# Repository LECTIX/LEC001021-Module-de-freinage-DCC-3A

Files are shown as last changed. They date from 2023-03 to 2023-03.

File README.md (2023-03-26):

# LEC001021-Module-de-freinage-DCC-3A
Fichiers sources pour le produit LEC001021

## Description du produit

Arrêtez et redémarrez vos convois de manière automatique et réaliste avec des arrêts et redémarrages progressifs des trains.
- **Technologie ABC**
- **Courrant maximum** de 3A.
- **Compatibilité DCC uniquement** (digital). Les décodeurs doivent être compatible avec la technologie ABC ([Cf. notice](docs/manual_fr.pdf)).

## Utiliser les fichiers sources pour fabriquer le produit

Il n'est **pas nécessaire de savoir souder ou d'être bon en électronique** pour se procurer ce produit. Grâce aux fichiers sources publiés ici, vous pouvez être en mesure de faire fabriquer ce produit par un sous traitant.

### Faire fabriquer chez un sous traitant

Il est aujourd'hui possible de faire fabriquer à moindre cout des cartes électroniques. Nous recommendons [JLCPCB](https://jlcpcb.com/) si vous voulez aller au moins cher. Si vous préférez un acteur européen, [eurocircuits](https://www.eurocircuits.com/) est un des acteurs reconnus.

IMAGE ALT TEXT (http://www.youtube.com/watch?v=RXGGvsUtz0c "TUTO : faire fabriquer un produit LECTIX")

1. Télécherger les sources de ce produit en cliquant sur le bouton `Code`, puis `Download ZIP`.
1. Décompresser le dossier.
1. Les fichiers pour la fabrication se trouvent dans le répertoire `hardware/prod`.
1. Se connecter sur [https://cart.jlcpcb.com/quote](https://cart.jlcpcb.com/quote)
1. Cliquer sur le bouton `Add gerber file` et sélectionner le fichier `gerbers.zip`.
1. Sélectionnez la quantité de cartes que vous souhaitez dans le champs `PCB Qty`.
1. Laisser toutes les autres options par défaut, puis cliquez sur le toggle switch en face de `PCB Assembly`, et enfin sur le bouton `confirm`.
1. Une preview de la carte électronique sans les composants doit apparaitre. Cliquez sur `NEXT`.
1. Cliquez sur le bouton `Add BOM File`, puis sélectionnez le fichier `bom.csv`
1. Cliquez sur le bouton `Add CPL File`, puis sélectionnez le fichier `pos.csv`
1. **Vérifier que tous les composants sont en stock** et bien sélectionnés, puis cliquez sur `NEXT`.
1. Une preview de la carte avec ses composants apparait. Continuer le chemin en cliquant sur `NEXT`.
1. Le prix final apparait. Sélectionnez la catégorie du produit, puis cliquez sur `SAVE TO CART`.
1. Une fois sauvegardé dans votre panier, vous pouvez valider votre commande et choisir le moyen d'acheminement. Afin de ne pas avoir à se préoccuper des frais de douane, nous vous conseillons de choisir une méthode d'expédition DDP.

Vous receverez vos cartes sous 1 à 3 semaines. 

**Nous ne sommes en aucun cas responsables des cartes qui arriveraient défectueuses ou non fonctionnelles.**

### Modifications des fichiers sources

Installez kicad 6 (ou version supérieure), et ouvrez le fichier LEC001021.kicad_pro

### Regénérer les fichiers gerber, BOM, et position (Optionnel)

Peut se faire simplement en utilisant kikit :

```
cd hardware

docker run --rm -w /kikit -v $PWD:/kikit yaqwsx/kikit kikit fab jlcpcb --assembly --no-drc --schematic LEC001021.kicad_sch --field LCSC --corrections JLCPCB_CORRECTION --nametemplate LEC001021_{} LEC001021.kicad_pcb prod/

```
## Notices
[Manuel FR](docs/manual_fr.pdf)

[Manuel EN](docs/manual_en.pdf)

[Manuel DE](docs/manual_de.pdf)
## License
Tous nos fichiers sont plubliés sous la license CERN Open Hardware Licence Version 2 - Strongly Reciprocal

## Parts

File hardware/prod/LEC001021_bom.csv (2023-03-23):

Comment | Designator | Footprint | LCSC
RS3M | D1,D2,D4,D5 | Diode_SMD:D_SMC | C330389
SS34C | D3 | Diode_SMD:D_SMC | C13763
Screw_Terminal_01x02_blue | J1 | 0_connectors:TerminalBlock_bornier-2_P5.08mm-blue | C395882
logo_lectix_25mm | LOGO1 | 0_logos:Logo_10mm

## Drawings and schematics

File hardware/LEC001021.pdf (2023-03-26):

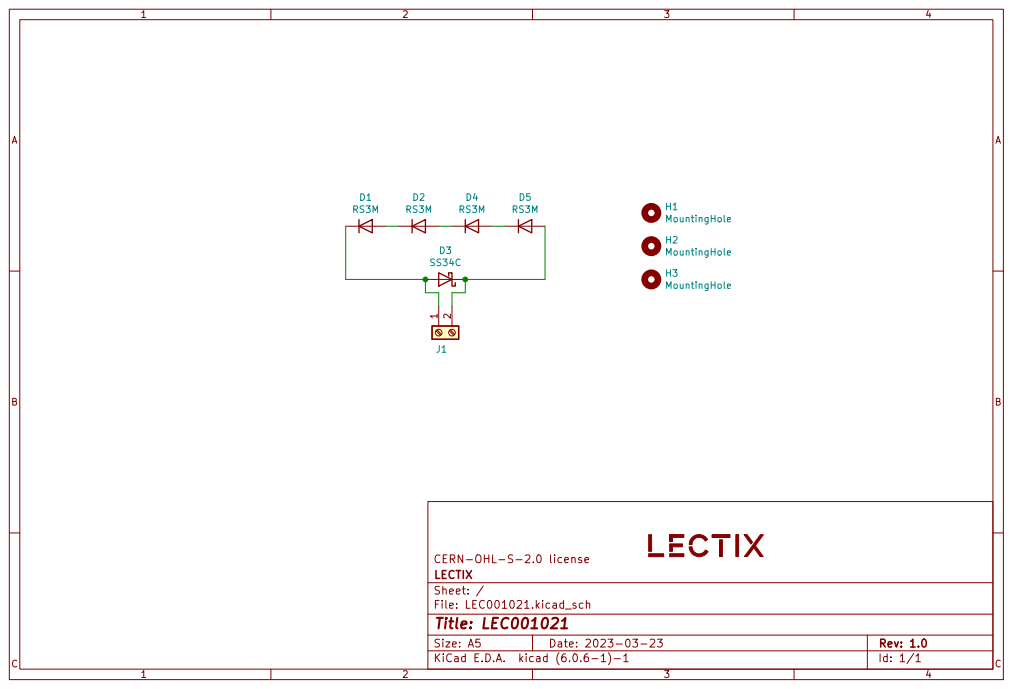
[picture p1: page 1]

File: LEC001021.kicad_sch Sheet: / LECTIX CERN-OHL-S-2.0 license D2 RS3M

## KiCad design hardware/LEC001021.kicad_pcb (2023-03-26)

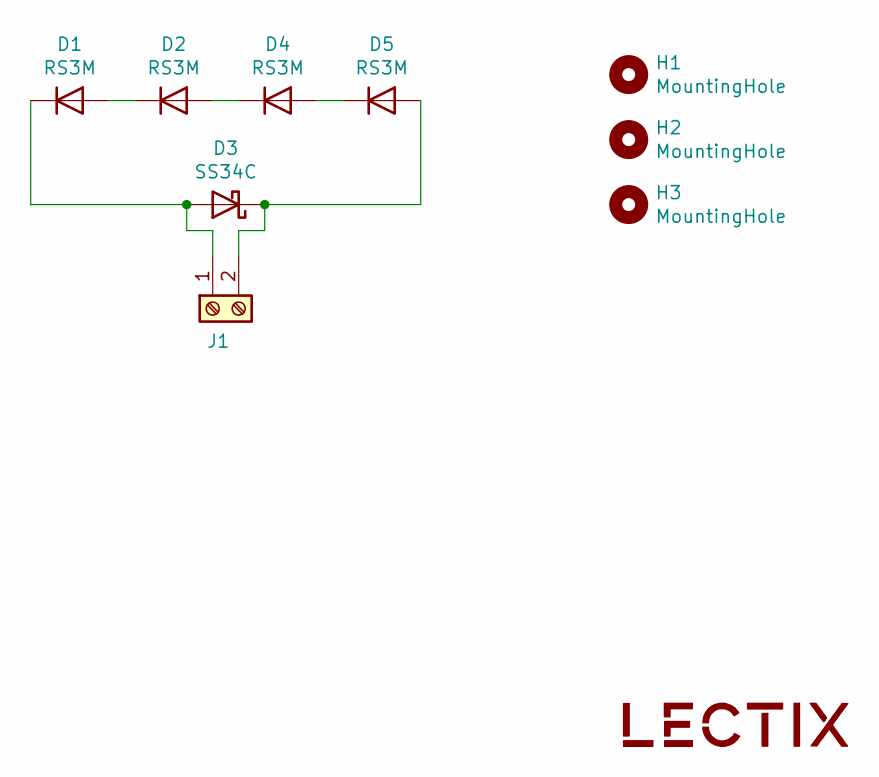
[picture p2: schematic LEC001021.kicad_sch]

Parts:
D1, D2, D4, D5: RS3M; D_SMC; MPN RS3M; LCSC C330389
D3: SS34C; D_SMC; MPN SS34C; LCSC C13763
H1, H2, H3: MountingHole; MountingHole_3.2mm_M3
J1: Screw_Terminal_01x02_blue; TerminalBlock_bornier-2_P5.08mm-blue; MPN DB301V-5.0-2P-BU-S; LCSC C395882
LOGO1: logo_lectix_25mm; Logo_10mm

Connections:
unnamed: D1.1 (K), D3.2 (A), J1.1
unnamed: D1.2 (A), D2.1 (K)
unnamed: D2.2 (A), D4.1 (K)
unnamed: D3.1 (K), D5.2 (A), J1.2
unnamed: D4.2 (A), D5.1 (K)

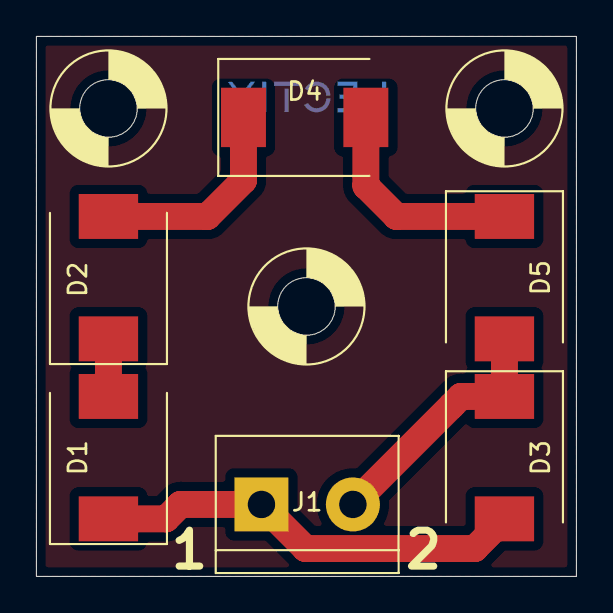
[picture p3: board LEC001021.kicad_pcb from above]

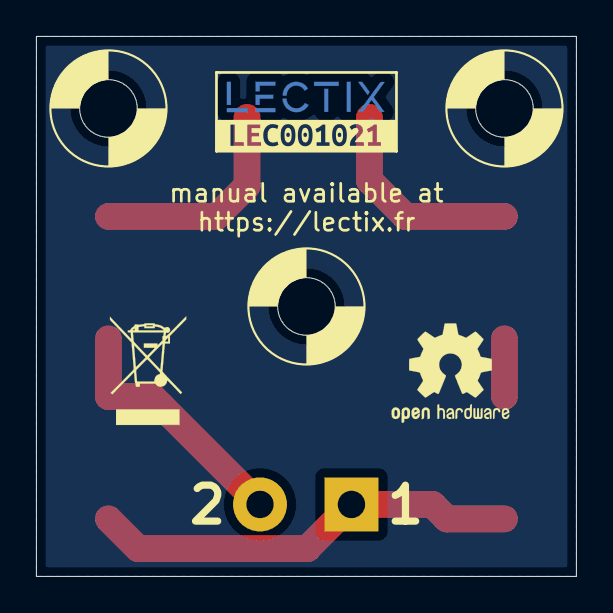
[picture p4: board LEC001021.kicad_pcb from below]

Board: 2 copper layers, 30.0 x 30.0 mm, 11 parts (2 on the bottom side), 5 nets.

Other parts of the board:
kibuzzard-6239BEEF: G***; kibuzzard-6239BEEF

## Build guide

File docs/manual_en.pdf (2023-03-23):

# DCC brake module

### LEC001021

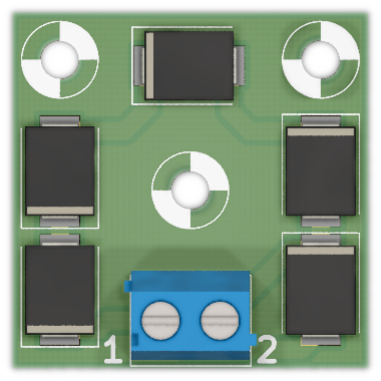
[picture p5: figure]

## 1 Overview

- Module equivalent to the BM1 module ref 22600 from Lenz.
- Allows the gradual stop and restart of trains running in a DCC environment.
- Maximum current of 3A
- ABC Breaking module for DCC only compatible with a few decoders (see section 4)
- 3 screw holes for easy mounting.

## 2 Applications

- Automatic stop of a convoy at the foot of a signal.
- Push-pull operation.
- Blocks systems - HO scale.
- Automatic stop when the railway switch is not properly set.
- Automatic stop at the station.

## 3 Technical specifications

Specification | Unit | Value
Maximum continuous current | A | 3
Maximum peak current (8.3 ms) | A | 100
Dimensions | mm | 30 * 30 * 13
Weight | g | 5

Table 1: Specifications

LEC001021 - DCC brake module rev 1.1.0 | 1

## 4 Compatibility

☞ Warning: this module only works in digital mode and is only compatible with decoders that support ABC technology. The table 2 shows a non-exhaustive list of decoders supporting ABC technology.

This module is recommended for the HO scale. For the N scale, use the LEC001020.

Brand | Compatible decoder | Manufacturer reference
Lenz | Gold maxi GOLD+ NEM652 GOLD+ mini NEM651 GOLD+ mini wired Silver+ NEM652 Silver+ direct Silver+ 21 Silver+ Plux12 Silver+ mini NEM651 Silver+ mini wired Standard+ V2 | 10440 10433-01 10411-01 10410-01 10331-01 10330-01 10321-01 10312-01 10311-01 / 10311-02 10310-01 10231-02
ESU | LokPilot V4 / V5 LokSound V4 / V5 | All LokPilot V4 and V5 All LokSound v4 and V5

Miniature decoders

MX620, MX620N, MX620R, MX620F MX618N18,MX621, MX621N, MX621R MX621, FMX622, MX622R, MX622F, MX622N

HO decoders

MX63, MX63R, MX63F, MX63T
MX623, MX623R, MX623F, MX623P12 MX630, MX630R, MX630F, MX630P16
zimo | Thin HO decoders | MX64, MX64R, MX64F, MX64T

High power HO decoders

MX64H, MX64HR, MX64HF, MX64V MX631, MX631R, MX631F, MX631D, MX631C MX632, MX632R, MX632D, MX632C, MX632V MX632W, MX632VD, MX632WD
MX633, MX633R, MX633F, MX633P22
Miniature sound decoders | MX648, MX648R, MX648F, MX648P16
| MX646, MX646R, MX646F, MX646N, MX646L
HO sound decoders | MX645, MX645R, MX645F, MX645P16
| MX645P22, MX644D, MX644C
tOm

(trainOmatic)

LOKCOMMANDER II | All decoders of the range.

Table 2: Compatible decoders

## 5 Usage

By generating an asymmetry in the DCC signal, this module allows compatible decoders to detect areas of slowdown or shutdown and react accordingly.

There are two steps to seing up this module: installation and wiring of the module and configuration of the decoder(s).

### 5.1 Installation and wiring of the module

Note: For optimal and safe operation, the wiring of this module must be done with a wire having a minimum section of 0.2mm²

The module must be wired as shown in the figure 1. The switch is optional. It allows the module to be shunted to manually restart the stopped train.

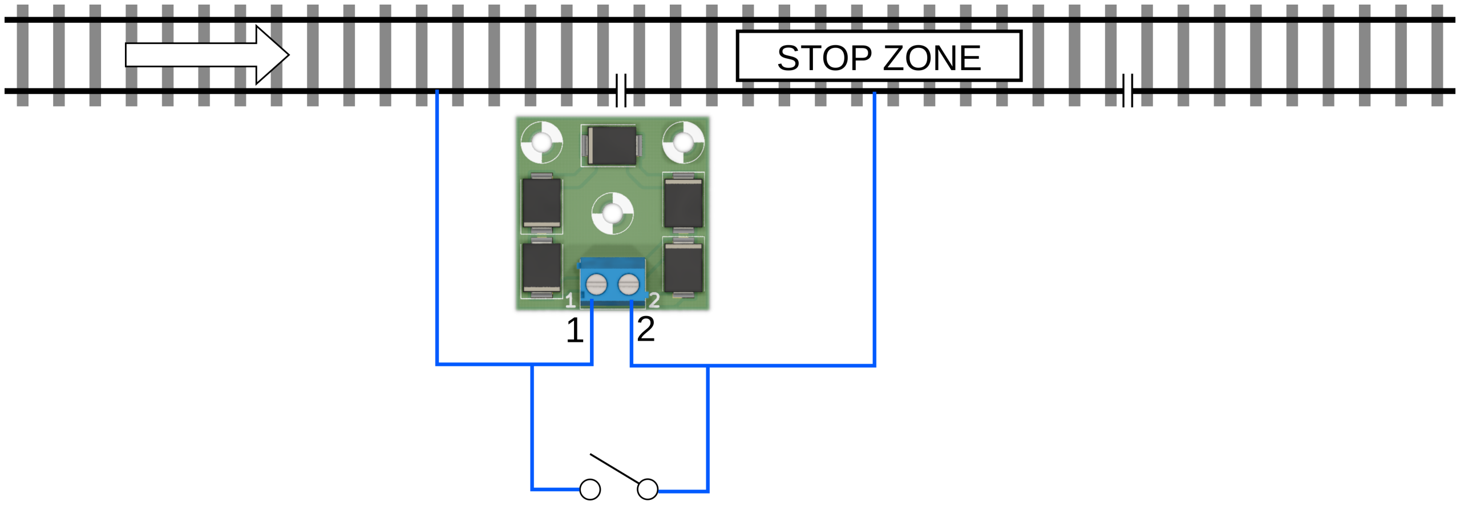
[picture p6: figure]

Figure 1: Wiring diagram for a stop zone controlled by a switch.

- When the switch is open, or there is simply no switch, a signal will be emied on the right rail of the stop zone, and any machine with a compatible and configured decoder will perform a stop procedure.
- When the switch is closed, no signal will be transmied at the stop area, so no train will stop in the area. If a train was stopped in the stop area, it will restart gradually.

☞ Note : The switch can be replaced by a relay, limit switch, or any other system with at least 1A breaking capacity.

### 5.2 Decoder configuration

To detect the ABC signal emied by this module, the decoders must be configured accordingly. The table 3 shows the CVs used to enable or modify the decoder’s behaviour towards the ABC signal.

### 5.2.1 Determining the decoder

If you know the type of decoder in your machine, go to the next section.

To identify the brand of your decoder, you need to read the value of CV8.

Brand | Lenz | ESU | Zimo | tOm
Value of CV8 identifying the manufacturer | 99 | 151 | 145 | 78

This table is not exhaustive, you will find a more complete list on the following link: hps://www.jmri.org/xml/XSLT/pages/DecoderId.html

### 5.2.2 ABC activated

☞ In any case, you will have to activate the ABC function of the decoder so that your trains can react to the signal emied by this module.

Brand | Lenz | ESU | Zimo | tOm
ABC braking, voltage higher on the right hand side | CV51 = 2 (bit 1) | CV27 = 1 (bit 0) | CV27 = 1 (bit 0) | CV27 = 1 (bit 0)
ABC braking, voltage higher on the le hand side | - | CV27 = 2 (bit 1) | CV27 = 2 (bit 1) | CV27 = 2 (bit 1)
Activation of ABC in both directions of travel | CV51 = 6 (bits 1 + 2) | CV27 = 3 (bits 0 + 1) | CV27 = 3 (bits 0 + 1) | CV27 = 3 (bits 0 + 1)

### 5.2.3 Testing the ABC signal detection

At this point, test if the machine detects the ABC stop signal.

☞ In some configurations, the machine may not detect the ABC stop signal correctly. Some decoder brands oer additional seings to address this issue.

Brand | Lenz | ESU | Zimo | tOm
ABC Detection threshold | - | CV134 = (4 ≤ val ≤ 32) | CV134 = (101 ≤ val ≤ 114) | CV141 = (8 ≤ val ≤ 16)
Compensation for ABC signal sensing error | - | CV102 = (0 ≤ val ≤ 255) | CV142 = (0 ≤ val ≤ 255) | -

### 5.2.4 Activate constant braking distance

The constant braking distance is the seing that allows a train to stop within a certain distance, regardless of its speed. Although not mandatory, this seing is strongly recommended for optimal operation.

Brand | Lenz | ESU | Zimo | tOm
Activation of constant braking dis-tance | CV51 += 1 (bit 0) | - | CV140 = 1 | CV27 += 128 (bit 7)
Braking length | CV52 = (0 ≤ val ≤ 255) | CV254 = (1 ≤ val ≤ 255) | CV141 = (0 ≤ val ≤ 255) | CV64 = (1 ≤ val ≤ 255)

☞ The ’+=’ sign means that the value given in the table must be added to the one previously set.

### 5.2.5 CV Summary for ABC

Brand | CV | bit | Function
Lenz | 51 | 0 1 ABC activated 2 3 4 | Activation of the constant braking distance ABC direction-dependency deactivated Activate push-pull operation with intermediate stop Activate push-pull operation without intermediate stop
| 52 | - | Braking length at constant braking distance activated
ESU | 27 | 0 1 ABC braking, voltage higher on the le hand side | ABC braking, voltage higher on the right hand side
| 102 | - | Compensation for ABC signal sensing error
| 134 | - | ABC Detection threshold
| 254 | - | Constant braking distance
zimo | 27 | 0 1 ABC braking, voltage higher on the le hand side | ABC braking, voltage higher on the right hand side
| 134 | - | ABC Detection threshold
| 140 | 0 | Activation of the constant braking distance function
| 141 | - | Constant braking distance
| 142 | - | Compensation for ABC signal sensing error
tOm | 27 | 0 ABC braking, voltage higher on the right hand side 1 ABC braking, voltage higher on the le hand side 7 | Activation of the constant braking distance function
| 64 | - | Constant braking distance
| 141 | - | ABC Detection threshold

Table 3: CV for ABC

Note : if the maneuver mode or the reduced run mode is activated, the decoder will ignore the ABC signals.

## 6 Dimensions

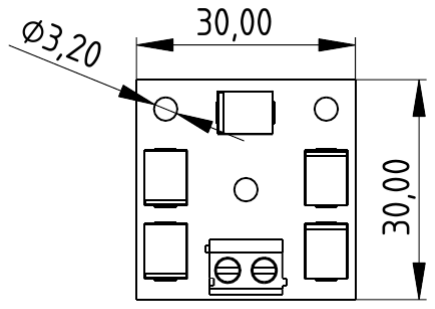
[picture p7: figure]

Figure 2: Dimensions of the module (all dimensions in mm).

## 7 Contact and support

For further information, please contact contact@lectix.fr.

## 8 Revision History

Revision | Date | Author(s) | Description
1.0.0 | 01.05.21 | TFC | Creation of the document
1.0.1 | 14.05.22 | TFC | Adding compatible decoders
1.1.0 | 30.05.22 | TFC | Added clarification in section 5.2

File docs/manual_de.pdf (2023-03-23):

# DCC Bremsmodul

### LEC001021

## 1 Eigenschaen


- Das Modul ist gleichwertig mit dem Modul BM1, Ref. 22600 von Lenz.
- Ermöglicht das schriweise Anhalten und Wiederanfahren von Zügen, die in einer DCC-Umgebung fahren.
- Maximaler Strom von 3A
- DCC-Bremsmodul | mit | ABC-
Technologie nur mit bestimmten Decodern kompatibel (siehe Abschni 3)
- 3 Schraublöcher für eine einfache Montage.

## 2 Anwendungen

- Automatisches Anhalten eines Konvois vor einem Signal.
- Pendelbetrieb (bei kompatiblen Decodern)
- Kantone.
- Automatischer Stopp, wenn der Weiche nicht richtig positioniert ist.
- Automatischer Halt am Bahnhof.

## 3 Kompatibilität

Achtung: Dieses Modul funktioniert nur im digitalen Modus und ist nur mit Decodern kompatibel, die die ABC-Technologie unterstützen. Die Tabelle 1 enthält eine nicht erschöpfende Liste von Decodern, die die ABC-Technologie unterstützen.

LEC001021 - DCC Bremsmodul rev 1.0.0 | 1

Marke | Kompatibler Decoder | Hersteller-Referenz
Lenz | Gold maxi GOLD+ NEM652 GOLD+ mini NEM651 GOLD+ mini wired Silver+ NEM652 Silver+ direct Silver+ 21 Silver+ Plux12 Silver+ mini NEM651 Silver+ mini wired Standard+ V2 | 10440 10433-01 10411-01 10410-01 10331-01 10330-01 10321-01 10312-01 10311-01 / 10311-02 10310-01 10231-02
ESU | LokPilot V4 / V5 LokSound V4 / V5 | Alle LokPilot V4 und V5 Alle LokSound v4 und V5

zimo

Miniatur-Dekoder

MX620, MX620N, MX620R, MX620F MX618N18,MX621, MX621N, MX621R MX621, FMX622, MX622R, MX622F, MX622N

HO-Dekoder

MX63, MX63R, MX63F, MX63T
MX623, MX623R, MX623F, MX623P12 MX630, MX630R, MX630F, MX630P16
Dünne HO-Dekoder | MX64, MX64R, MX64F, MX64T

HO-Hochleistungsdekoder

MX64H, MX64HR, MX64HF, MX64V MX631, MX631R, MX631F, MX631D, MX631C MX632, MX632R, MX632D, MX632C, MX632V MX632W, MX632VD, MX632WD
MX633, MX633R, MX633F, MX633P22
Miniatur-Tondecoder | MX648, MX648R, MX648F, MX648P16
| MX646, MX646R, MX646F, MX646N, MX646L
HO-Sounddecoder | MX645, MX645R, MX645F, MX645P16
| MX645P22, MX644D, MX644C

Table 1 – Kompatible Decoder

## 4 Technische Daten

Spezifikation | Einheit | Wert
Maximaler Dauerstrom | A | 3
Maximaler Spitzenstrom (8,3 ms) | A | 100
Abmessungen | mm | 25 * 20 * 13
Gewicht | g | 3.1

Table 2 – Spezifikationen

## 5 Verwenden Sie

Durch die Erzeugung einer Asymmetrie im DCC-Signal ermöglicht dieses Modul kompatiblen Decodern, Bereiche der Verlangsamung oder Abschaltung zu erkennen und entsprechend zu

reagieren.

Die Einrichtung dieses Moduls erfolgt in zwei Schrien: Einbau und Verdrahtung des Moduls und Konfiguration des/der Decoder(s).

### 5.1 Einbau und Verdrahtung des Moduls

Hinweis: Für einen optimalen und sicheren Betrieb muss dieses Modul mit einer Mindestquerschnisfläche von 0,2mm²
verdrahtet werden.

Das Modul muss wie in Abbildung 1 dargestellt verdrahtet werden. Der Schalter ist optional. Damit kann das Modul umgangen werden, um den angehaltenen Zug manuell wieder in Gang zu setzen.

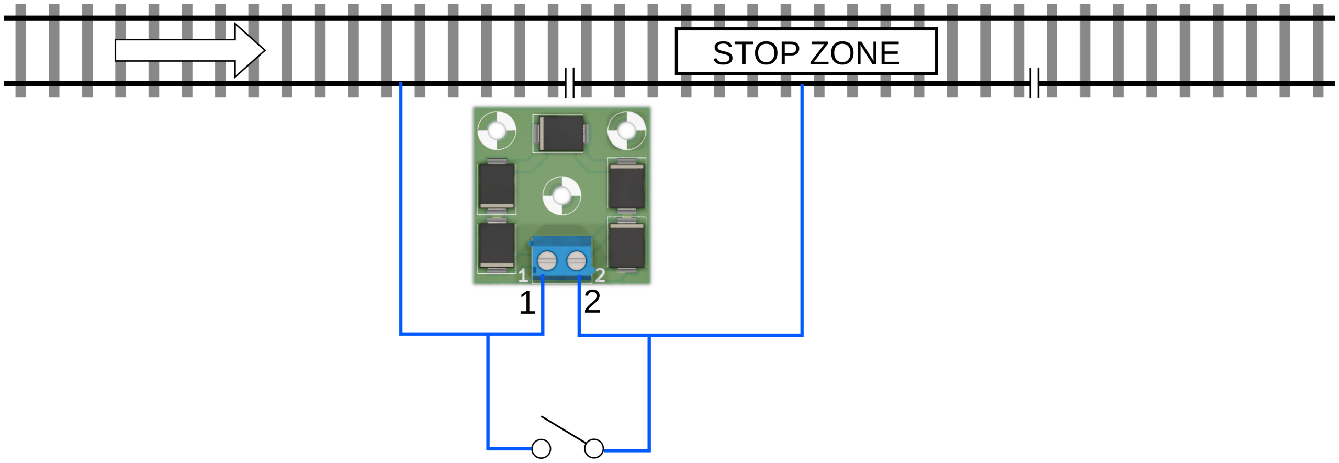
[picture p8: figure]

Figure 1 – Schaltplan für eine schaltergesteuerte Stoppzone.

- Wenn die Schalter geönet sind oder einfach kein Schalter vorhanden ist, wird ein Signal auf der rechten Schiene des Haltebereichs ausgegeben, und jede Maschine mit einem kompatiblen und konfigurierten Decoder führt einen Stoppvorgang aus.
- Wenn der Schalter geschlossen ist, wird im Haltestellenbereich kein Signal übertragen, so dass kein Zug in diesem Bereich halten kann. Wenn ein Zug im Haltestellenbereich angehalten wurde, wird er schriweise wieder angefahren.

☞ Hinweis: Der Schalter kann durch ein Relais, einen Endschalter oder ein anderes System mit einer Schaltleistung von mindestens 1 A ersetzt werden.

### 5.2 Decoder-Konfiguration

Um das von diesem Modul ausgegebene ABC-Signal zu erkennen, müssen die Decoder entsprechend konfiguriert werden. Die Tabelle eftab:cv zeigt die CVs, mit denen das Verhalten des Decoders in Bezug auf das ABC-Signal aktiviert oder verändert werden kann.

In jedem Fall müssen Sie die ABC-Funktion des Decoders aktivieren, damit Ihre Züge auf das Signal dieses Moduls reagieren können.

Marke | CV | bit | Funktion
Lenz | 51 | 0 1 ABC aktiviert 2 3 4 | Konstanter Bremsweg aktiviert Richtungsabhängigkeit von ABC ist ausgeschaltet Pendelbetrieb ohne Zwischenhalt aktivieren Pendelbetrieb mit Zwischenhalt aktivieren
| 52 | - | Bremsweg bei aktiviertem konstanten Bremsweg
| 54 | - | Aufenthaltsdauer bei Pendelbetrieb, 1 bis 256 Sekunden
ESU | 27 | 0 1 Aktivierung von ABC in umgekehrter Richtung | Aktivierung des ABC in der herkömmlichen Fahrtrichtung
| 134 | - | Erkennungsschwelle ABC
| 254 | - | Konstanter Bremsweg
zimo | 27 | 0 1 Aktivierung von ABC in umgekehrter Richtung | Aktivierung des ABC in der herkömmlichen Fahrtrichtung
| 134 | - | Erkennungsschwelle ABC
| 140 | 0 | Aktivierung der Funktion des konstanten Bremswegs
| 141 | - | Konstanter Bremsweg
| 142 | - | Hochgeschwindigkeits-Kompensation der ABC-Erkennungsschwelle

Table 3 – CV für ABC

Hinweis: Wenn der Manövriermodus oder der reduzierte Fahrmodus aktiviert ist, ignoriert der Decoder die ABC-Signale.

## 6 Abmessungen

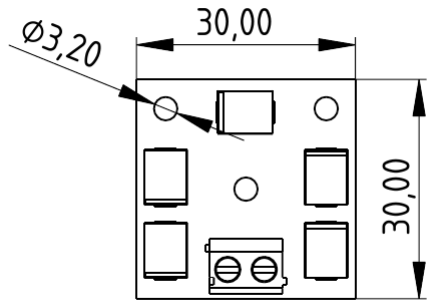
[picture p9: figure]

Figure 2 – Abmessungen des Anschlagmoduls (alle Maße in mm).

## 7 Kontakt und Service

Für weitere Informationen wenden Sie sich bie an contact@lectix.fr.

## 8 Revision History

Revision | Date | Author(s) | Description
1.0.0 | 01.05.21 | TFC | Erstellung des Dokuments

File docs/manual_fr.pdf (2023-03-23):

# Module de freinage DCC

### LEC001021

## 1 Caractéristiques


- Module équivalent au module BM1 ref 22600 de Lenz.
- Permet l’arrêt et le redémarrage progressif des trains en digital.
- Courrant maximum de 3A
- Module de freinage DCC utilisant la technologie ABC compatible uniquement avec certains décodeurs (Cf. section 4)
- 3 trous de fixation pour un montage facile.

## 2 Applications

- Arrêt automatique d’un convoi au pied d’un signal.
- Va et vient automatique.
- Cantons à l’échelle HO.
- Arrêt automatique lorsque l’aiguillage n’est pas bien positionné.
- Arrêt automatique en gare.

## 3 Specifications technique

Specification | Unité | Valeur
Courant maximum en continu | A | 3
Courant maximum en pointe (8.3 ms) | A | 100
Dimensions | mm | 30 * 30 * 13
Poids | g | 5

Table 1: Spécifications

LEC001021 - Module de freinage DCC rev 1.1.0 | 1

## 4 Compatibilité

☞ Aention : ce module ne fonctionne qu’en digital et n’est compatible qu’avec les décodeurs qui supportent la technologie ABC. Le tableau 2 montre une liste non exhaustive de décodeurs supportant la technologie ABC.

Ce module est recommandé pour l’échelle HO. Pour l’échelle N, privilégiez plutôt le module LEC001020.

Marque | Décodeur compatible | Référence fabricant
Lenz | Gold maxi GOLD+ NEM652 GOLD+ mini NEM651 GOLD+ mini wired Silver+ NEM652 Silver+ direct Silver+ 21 Silver+ Plux12 Silver+ mini NEM651 Silver+ mini wired Standard+ V2 | 10440 10433-01 10411-01 10410-01 10331-01 10330-01 10321-01 10312-01 10311-01 / 10311-02 10310-01 10231-02
ESU | LokPilot V4 / V5 LokSound V4 / V5 | Tous les LokPilot V4 et V5 Tous les LokSound v4 et V5

Décodeurs miniature

MX620, MX620N, MX620R, MX620F MX618N18,MX621, MX621N, MX621R MX621, FMX622, MX622R, MX622F, MX622N

Décodeurs HO

MX63, MX63R, MX63F, MX63T
MX623, MX623R, MX623F, MX623P12 MX630, MX630R, MX630F, MX630P16
zimo | Décodeurs HO faible épaisseur | MX64, MX64R, MX64F, MX64T

Décodeurs HO forte puissance

MX64H, MX64HR, MX64HF, MX64V MX631, MX631R, MX631F, MX631D, MX631C MX632, MX632R, MX632D, MX632C, MX632V MX632W, MX632VD, MX632WD
MX633, MX633R, MX633F, MX633P22
Décodeurs sonores miniature | MX648, MX648R, MX648F, MX648P16
| MX646, MX646R, MX646F, MX646N, MX646L
Décodeurs sonores HO | MX645, MX645R, MX645F, MX645P16
| MX645P22, MX644D, MX644C
tOm

(trainOmatic)

LOKCOMMANDER II | Tous les décodeurs de la gamme.

Table 2: Décodeurs compatibles

## 5 Utilisation

En générant une asymétrie dans le signal DCC, ce module permet aux décodeurs compatibles de détecter des zones de ralentissement ou d’arrêt et de réagir en conséquence.

La mise en place de ce module se fait en deux étapes : l’installation et le câblage du module, puis la configuration du ou des décodeurs.

### 5.1 Installation et câblage du module

Remarque : pour un fonctionnement optimal et sans danger, le câblage de ce module doit se faire avec un fil possédant une section minimale de 0.2mm²

Le module doit être câblé tel que sur la figure 1. L’interrupteur est optionnel. Il permet de shunter le module pour faire repartir manuellement le train arrêté.

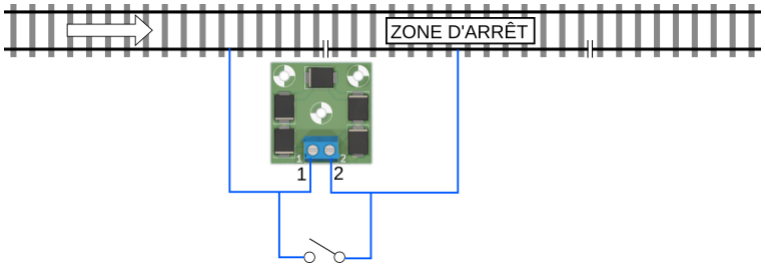
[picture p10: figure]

Figure 1: Schéma de câblage pour une zone d’arrêt contrôlée par un interrupteur.

- Lorsque l’interrupteur est ouvert, ou qu’il n’y a tout simplement pas d’interrupteur, un signal sera émis sur le rail droit de la zone d’arrêt, et toute machine équipée d’un décodeur compatible et configuré exécutera une procédure d’arrêt.
- Lorsque l’interrupteur est fermé, aucun signal ne sera transmit au niveau de la zone d’arrêt, aucun train ne s’arrêtera donc dans la zone. Si un train était arrêté dans la zone d’arrêt, il redémarrera progressivement.

☞ Note : L’interrupteur peut être remplacé par un relais, un interrupteur fin de course, ou par tout autre système ayant un pouvoir de coupure d’au moins 1A.

### 5.2 Configuration du décodeur

Pour détecter le signal ABC émis par ce module, les décodeurs doivent être configurés en conséquence. Le tableau 3 montre les CV utilisées pour activer ou modifier le comportement du décodeur vis à vis du signal ABC.

### 5.2.1 Détermination du décodeur

Si vous connaissez le type de décodeur présent dans votre machine, passez à la section suivante.

Pour identifier la marque de votre décodeur, il faut lire la valeur du CV8.

Marque | Lenz | ESU | Zimo | tOm
Valeur du CV8 identifiant le constructeur | 99 | 151 | 145 | 78

Ce tableau est non exhaustif, vous retrouverez une liste plus complète sur le lien suivant : hps://www.jmri.org/xml/XSLT/pages/DecoderId.html

### 5.2.2 Activation de l’ABC

☞ Dans tous les cas, il vous faudra activer la fonction ABC du décodeur pour que vos train puissent réagir au signal émis par ce module.

Marque | Lenz | ESU | Zimo | tOm
Activation de l’ABC dans le sens de marche classique | CV51 = 2 (bit 1) | CV27 = 1 (bit 0) | CV27 = 1 (bit 0) | CV27 = 1 (bit 0)
Activation de l’ABC dans le sens de marche inverse | - | CV27 = 2 (bit 1) | CV27 = 2 (bit 1) | CV27 = 2 (bit 1)
Activation de l’ABC dans les deux sens de marche | CV51 = 6 (bits 1 + 2) | CV27 = 3 (bits 0 + 1) | CV27 = 3 (bits 0 + 1) | CV27 = 3 (bits 0 + 1)

### 5.2.3 Tester la détection du signal ABC

A ce stade, tester si la machine détecte bien le signal d’arrêt ABC.

☞ Dans certaines configurations, la machine peut ne pas détecter correctement le signal d’arrêt ABC.
Certaines marques de décodeur proposent des paramètres de réglage supplémentaires pour répondre à ce problème.
Marque | Lenz | ESU | Zimo | tOm
Seuil de détection ABC | - | CV134 = (4 ≤ val ≤ 32) | CV134 = (101 ≤ val ≤ 114) | CV141 = (8 ≤ val ≤ 16)
Compensation erreur captage ABC | - | CV102 = (0 ≤ val ≤ 255) | CV142 = (0 ≤ val ≤ 255) | -

### 5.2.4 Activer la distance de freinage constante

La distance de freinage constante est le réglage permeant à un train de s’arrêter sur une distance déterminée, quelque soit sa vitesse. Bien que non obligatoire, ce paramètre est fortement recommandé pour un fonctionnement optimal.

Marque | Lenz | ESU | Zimo | tOm
Activation distance de freinage con-stante | CV51 += 1 (bit 0) | - | CV140 = 1 | CV27 += 128 (bit 7)
Longueur de freinage | CV52 = (0 ≤ val ≤ 255) | CV254 = (1 ≤ val ≤ 255) | CV141 = (0 ≤ val ≤ 255) | CV64 = (1 ≤ val ≤ 255)

☞ Le signe ’+=’ signifie qu’il faut additionner la valeur donnée dans le tableau avec celle configurée auparavant.

### 5.2.5 Récapitulatif CV pour l’ABC

Marque | CV | bit | Fonction
Lenz | 51 | 0 1 Activation de l’ABC 2 3 4 | Activation de la distance de freinage constante si = 1, prise en compte du signal ABC dans les deux sens de marche Activation du mode va et vient avec arrêt intermédiare Activation du mode va et vient sans arrêt intermédiaire
| 52 | - | Longueur de freinage en cas de distance de freinage constante activée
ESU | 27 | 0 1 Activation de l’ABC dans le sens de marche inverse | Activation de l’ABC dans le sens de marche classique
| 102 | - | Compensation erreur captage ABC
| 134 | - | Seuil de détection ABC
| 254 | - | Distance de freinage constante
zimo | 27 | 0 1 Activation de l’ABC dans le sens de marche inverse | Activation de l’ABC dans le sens de marche classique
| 134 | - | Seuil de détection ABC
| 140 | 0 | Activation de la fonction distance de freinage constante
| 141 | - | Distance de freinage constante
| 142 | - | Compensation erreur captage ABC
tOm | 27 | 0 Activation de l’ABC dans le sens de marche classique 1 Activation de l’ABC dans le sens de marche inverse 7 | Activation de la fonction distance de freinage constante
| 64 | - | Distance de freinage constante
| 141 | - | Seuil de détection ABC

Table 3: CV pour l’ABC

Remarque : si le mode manoeuvre ou le mode marche réduite est activé, le décodeur ne tiendra pas compte des signaux ABC.

## 6 Dimensions


Figure 2: Dimensions du module d’arrêt (toutes les côtes sont données en mm).

## 7 Contact et SAV

Pour tout renseignement, veuillez vous adresser à contact@lectix.fr.

## 8 Revision History

Revision | Date | Author(s) | Description
1.0.0 | 01.05.21 | TFC | Création du document
1.0.1 | 14.05.22 | TFC | Ajout de décodeurs compatibles
1.1.0 | 30.05.22 | TFC | Ajout de précisions dans la section 5.2

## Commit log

2023-03-23 chore: Add product sources
    [LEC001021-CmtUser.gbr, LEC001021-CuBottom.gbl, LEC001021-CuTop.gtl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]
2023-03-23 docs: Add reference to kicad
2023-03-26 chore: Add prefix to prod files + put them directly into prod directory instead of in a subdirectory
    [LEC001021-CmtUser.gbr, LEC001021-CuBottom.gbl, LEC001021-CuTop.gtl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]
2023-03-26 Add OSHW logo
    [LEC001021-CmtUser.gbr, LEC001021-CuBottom.gbl, LEC001021-CuTop.gtl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]
2023-03-26 Add pdf schematic file
    [LEC001021.kicad_sch]
